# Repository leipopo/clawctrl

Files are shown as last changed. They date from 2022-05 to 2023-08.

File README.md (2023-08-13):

# An end effector 

using a specific protocol（see in code file） on uart to control a four fingers hand moving to a certain position or use a constant force to garb a object

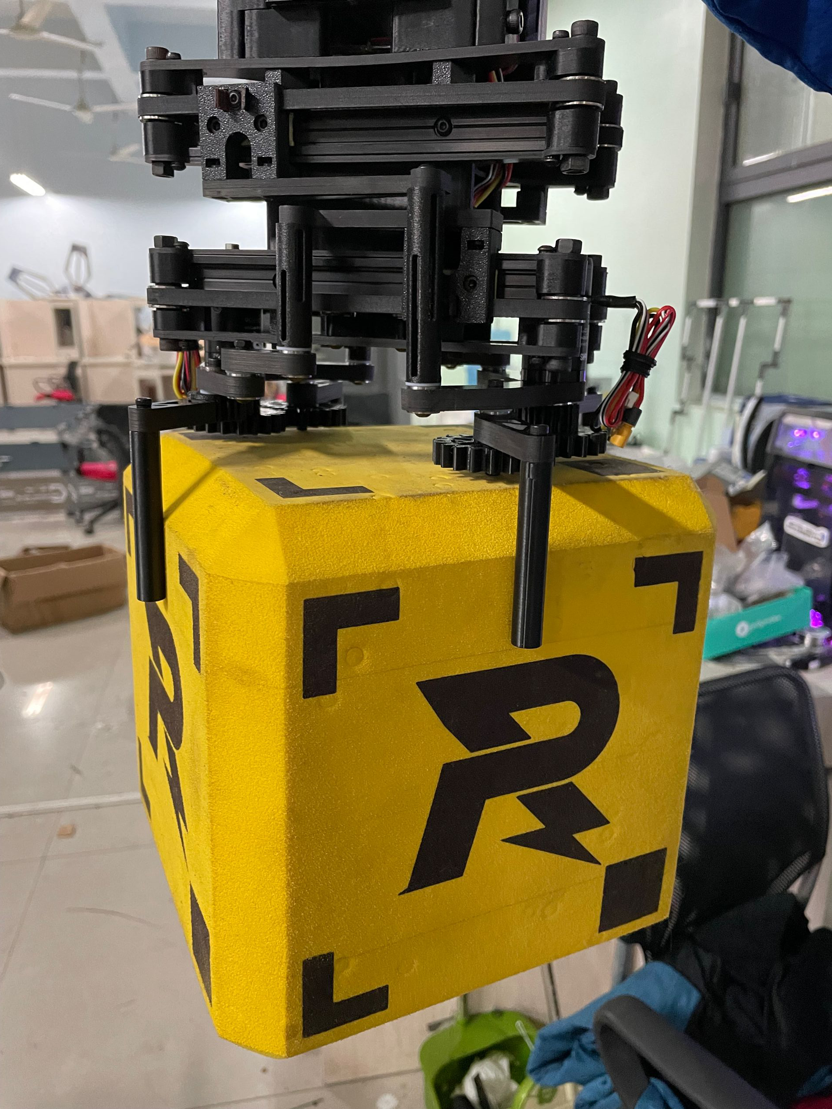
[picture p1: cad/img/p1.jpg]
claw with a RoboMaster gold ore without ctrl


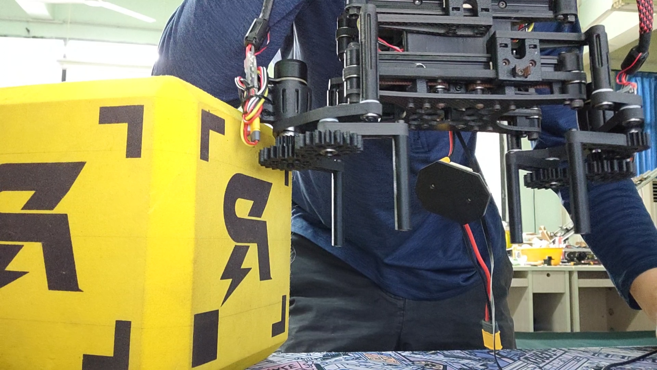
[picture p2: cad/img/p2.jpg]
claw with a RoboMaster gold ore


# Built with 
RoboMaster m2006&c610 kit

3d_printed abs and pet-cf (filament from Fusrock)

cnc carbon fibre sheet 
            
# Coded on 
a stm32(RoboMaster aboard with f427) with MDK and cubemx 

# Content

cad contains .stp and .stl

code contains code generated by cubemx

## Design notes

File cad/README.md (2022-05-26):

# content
## process（除张紧臂及（mir）外，全部一式两份，张紧臂及（mir）四份）
- v3打印件： 打印件stl文件 
            打印件设计优化过 使用fdm工艺打印不需要添加支撑
            stl已放置至合适方向 
            建议壁厚大于2mm 填充大于百分之三十 直线或网格填充
- v3板件：板件step文件 有沉孔 须向加工商注明
- bom表：还没写

## cad 
- lastest version step and f3d

## img
- some imgs.jpg

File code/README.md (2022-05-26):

# 参数单位：（详见config.h）
- 角度：deg
- 转速：rpm
- 电流：A
- 转矩：N·m
- 时间：ms
- 频率：Hz

# 电机定义：
- 手指电机为电机一与电机二
- 手掌电机为电机三（远离手指）和电机四（靠近手指）

# 基本通讯：
## PCtoMCU：

|Data[0]|Data[1]|Data[2]|Data[3]|Data[4]|Data[5]|Data[6]|Data[7]|Data[8]|Data[9]|Data[10]|Data[11]| 功 能  |
|:----:|:----:|:----:|:----:|:----:|:----:|:----:|:----:|:----:|:----:|:----:|:----:|:----:|
|0x00|电机一相对角度改变值高八位|电机一相对角度改变值低八位|电机二相对角度改变值高八位|电机二相对角度改变值低八位|电机三相对角度改变值高八位|电机三相对角度改变值低八位|电机四相对角度改变值高八位| 电机四相对角度改变值低八位| 暂无校验| 暂无校验| 0x0A|设定电机相对角度|
|0x01|电机一绝对角度值高八位|电机一绝对角度值低八位|电机二绝对角度值高八位|电机二绝对角度值低八位|电机三绝对角度值高八位|电机三绝对角度值低八位|电机四绝对角度值高八位|电机四绝对角度值低八位| 暂无校验| 暂无校验| 0x0A|设定电机绝对角度|
|0x02|电机一速度设定值高八位|电机一速度设定值低八位|电机二速度设定值高八位|电机二速度设定值低八位|电机三速度设定值高八位|电机三速度设定值低八位|电机四速度设定值高八位|电机四速度设定值低八位| 暂无校验| 暂无校验| 0x0A|设定电机最大转速|
|0x03|电机一转矩值X10高八位|电机一转矩值X10低八位|电机二转矩值X10高八位|电机二转矩值X10低八位|电机三转矩值X10高八位|电机三转矩值X10低八位|电机四转矩值X10高八位|电机四转矩值X10低八位| 暂无校验| 暂无校验| 0x0A|设定电机转矩|
|0x04|0x00|0x00|0x00|0x00|0x00|0x00|0x00| 0x00| 暂无校验| 暂无校验| 0x0A|放松|
|0x05|0x00|0x00|0x00|0x00|0x00|0x00|0x00| 0x00| 暂无校验| 暂无校验| 0x0A|回零|
|0xff|0x00|0x00/0x01|0x00|0x00/0x01|0x00|0x00/0x01|0x00| 0x00/0x01| 0x0/10/10/10/1| 0x0/10/10/10/1| 0x0A|关电机|

**注：电机控制方式是同时变化的，**即爪子四个电机只能同时以绝对角度或者相对角度或者转矩控制，且只能同时放松或回零。
具体状态转换见（infoproc.c/infoproc.h，
  
`void command2clawinfo(usercommand *uc,clawinfo *ci,MotorInfo m[4])`，

`void motor2clawinfo(clawinfo *ci,MotorInfo m[4])`，

`void claw2motorinfo(clawinfo *ci,MotorInfo m[4])`)。

**电机通断电可以单独控制，** 如单独断开电机二的电流需输入0xff 0x00 0x01（电机一通电）0x00 0x00（电机二断电）0x00 0x01（电机三通电） 0x00 0x01（电机四通电） 0x10 0x11（校验） 0x0a，具体转换详见（uart3.c/uart3.h，

`void RX_Decoder(uint8_t *buf, usercommand *uc)`）。

串口接收见（uart3.c/uart3.h，
  
`void RX_Decoder(uint8_t *buf, usercommand *uc)`）。

## MCUtoPC：
### 数据回报：
- 状态定义：
- 爪子状态：0x00 rel_postionctrl 0x01 abs_postionctrl 0x02 torquectrl 0x03 loose 0x04 zero 0x05 ready 0x06 moving
- 电机状态：0x00 loose 0x01 zeroing 0x10 inpostion 0x11 moving

|Data[0]|Data[1]|Data[2]|Data[3]|Data[4]|Data[5]|Data[6]|Data[7]|Data[8]|Data[9]|Data[10]|Data[11]| 功 能  |
|:----:|:----:|:----:|:----:|:----:|:----:|:----:|:----:|:----:|:----:|:----:|:----:|:----:|
|0xf0|0x00|电机一状态|0x00|电机二状态|0x00|电机三状态|0x00| 电机四状态| 0x00| 爪子状态| 0x0A|回报电机当前状态和爪子状态|
|0xf1|当前电机一转矩X100高八位|当前电机一转矩X100低八位|当前电机二转矩X100高八位|当前电机二转矩X100低八位|当前电机三转矩X100高八位|当前电机三转矩X100低八位|当前电机四转矩X100高八位|当前电机四转矩X100低八位| 四电机转矩X100加和高八位| 四电机转矩X100加和高八位| 0x0A|回报电机当前转矩X100|
|0xf2|当前电机一角度高八位|当前电机一角度低八位|当前电机二角度高八位|当前电机二角度低八位|当前电机三角度高八位|当前电机三角度低八位|当前电机四角度高八位|当前电机四角度低八位| 四电机角度加和高八位| 四电机角度加和低八位| 0x0A|回报电机当前角度|
|0xf3|当前电机一速度高八位|当前电机一速度低八位|当前电机二速度高八位|当前电机二速度低八位|当前电机三速度高八位|当前电机三速度低八位|当前电机四速度高八位|当前电机四速度低八位| 四电机转速加和高八位| 四电机转速加和低八位| 0x0A|回报电机当前转速|

### 警告回报：

|Data[0]|Data[1]|Data[2]|Data[3]|Data[4]|Data[5]|Data[6]|Data[7]|Data[8]|Data[9]|Data[10]|Data[11]|
|:----:|:----:|:----:|:----:|:----:|:----:|:----:|:----:|:----:|:----:|:----:|:----:|
|0xaa|手掌电机差角过大警告|电机位置控制转警告高八位|电机位置控制转警告低八位|0x00|0x00|0x00|0x00|0x00|0x00|0x00|0x0a|

**注：在对手掌电机差角的判断中若电机三角度大于电机四（以回零的方向为正）则反馈0x10，反之为0x01，正常为0x00；
在对电机=堵转的判断中，若电机二堵转则反馈0x0100，正常为0x0000**

内容详见（infoproc.c/infoproc.h，

`void sendmestopc(void)`)。

电机控制算法详见（motorlib.c/motorlib.h）。

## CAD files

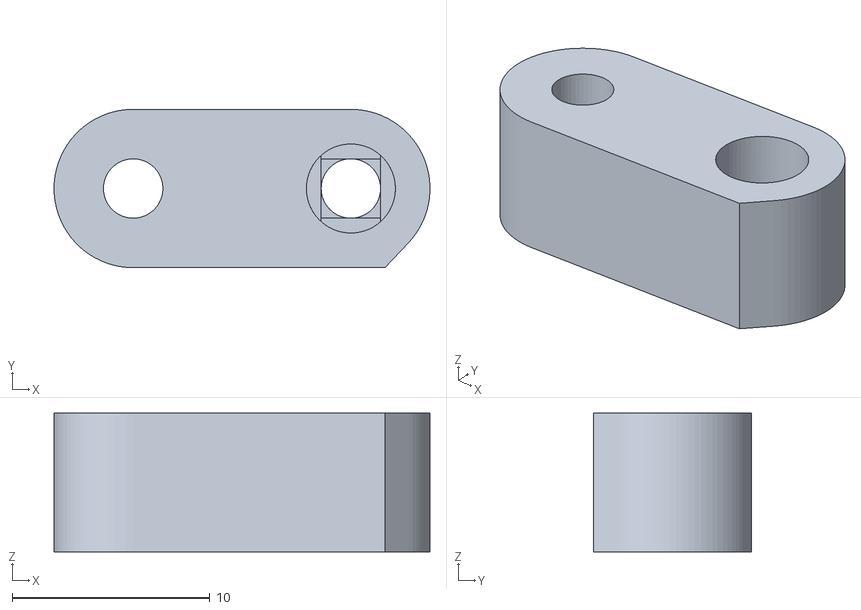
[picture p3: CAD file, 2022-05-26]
cad/prosfile/V3打印件/新张紧臂（mir） v2.stl
19.0 x 8.00 x 7.00

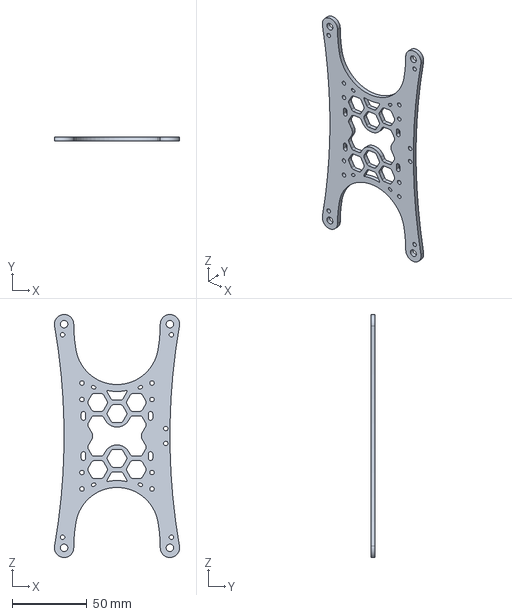
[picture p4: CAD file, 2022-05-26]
cad/prosfile/V3板件/上板 v11.step
84.0 x 3.00 x 163.0 mm

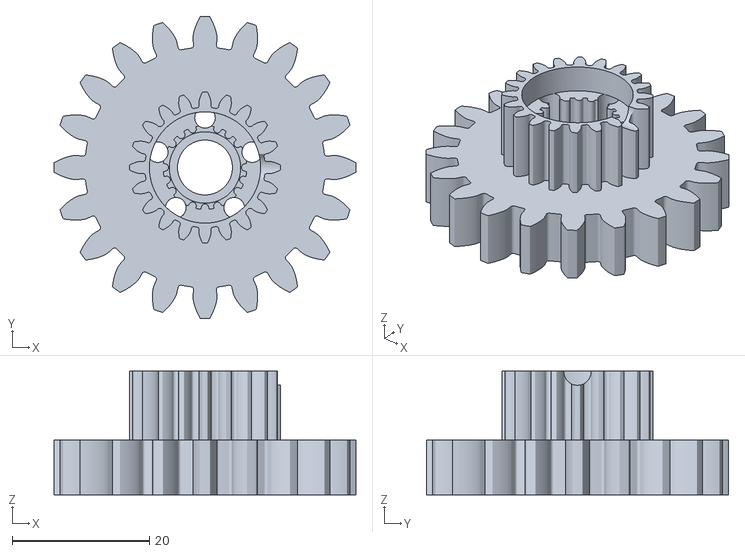
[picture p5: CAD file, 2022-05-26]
cad/prosfile/V3打印件/1_20&2_20驱动齿 v5.stl
44.0 x 44.0 x 18.0

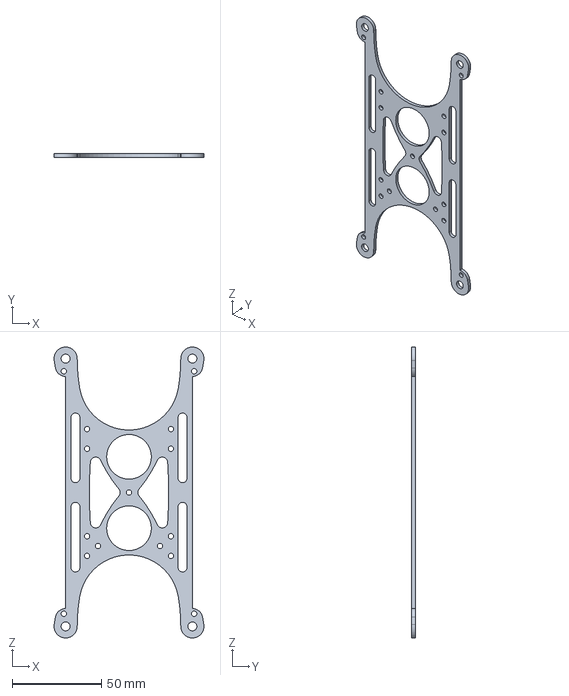
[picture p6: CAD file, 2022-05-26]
cad/prosfile/V3板件/下板 v13.step
84.0 x 2.00 x 163.0 mm

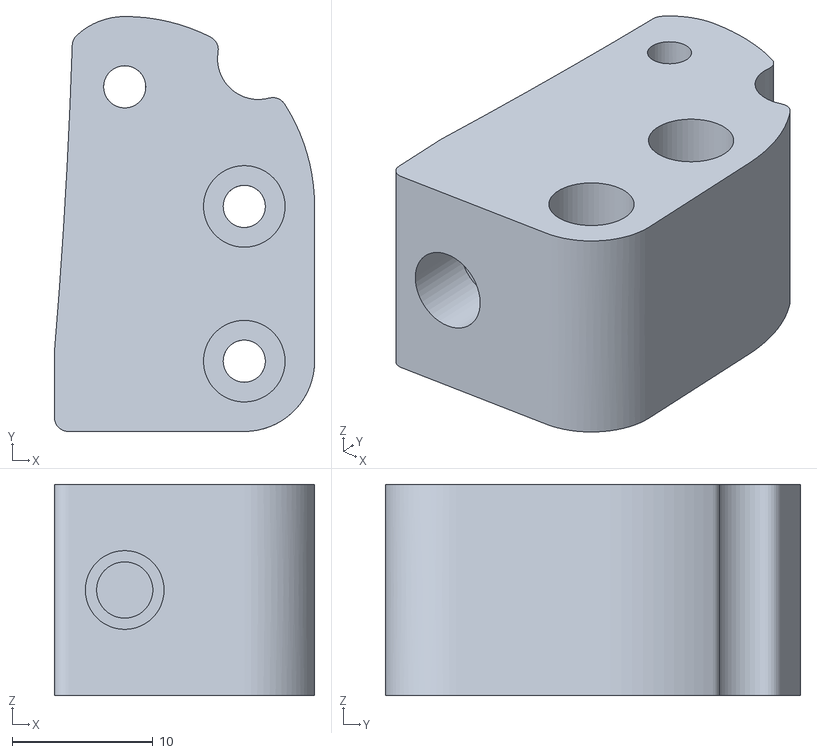
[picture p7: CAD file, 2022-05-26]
cad/prosfile/V3打印件/锚点 v4.stl
18.5 x 29.5 x 15.0

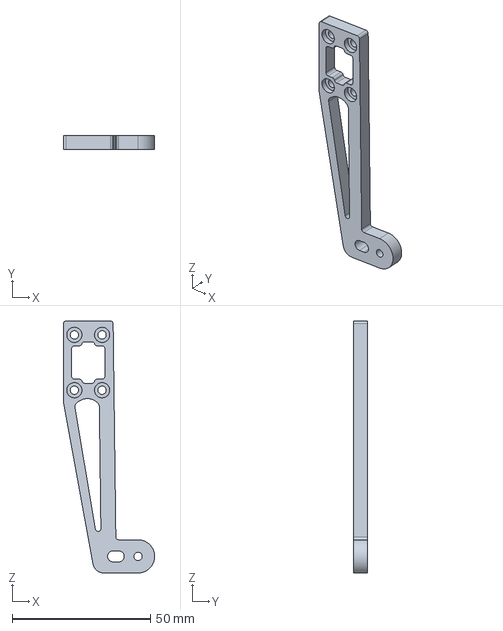
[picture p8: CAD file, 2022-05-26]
cad/prosfile/V3板件/效应器推杆 v13.step
33.0 x 5.00 x 91.0 mm

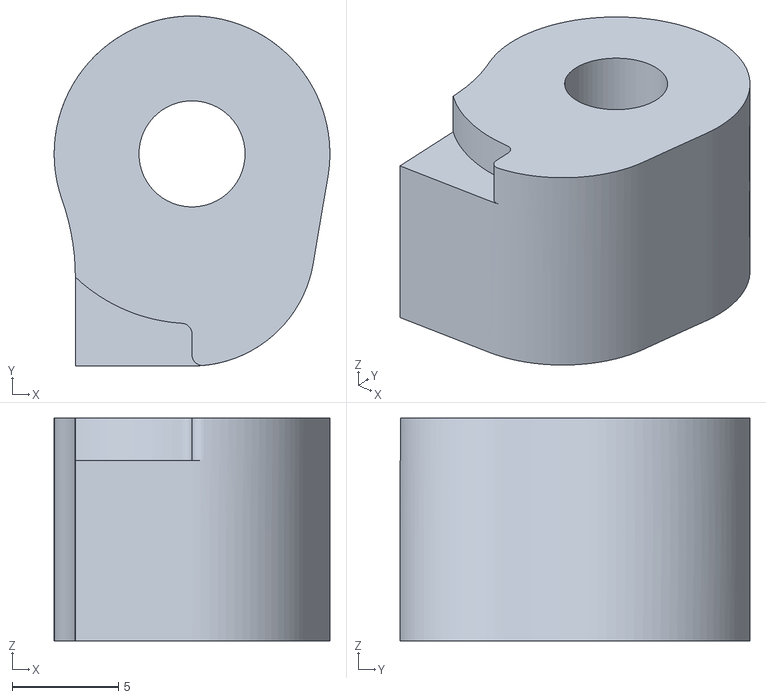
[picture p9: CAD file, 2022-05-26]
cad/prosfile/V3打印件/同步带角导向下mirror v2.stl
13.0 x 16.5 x 10.5

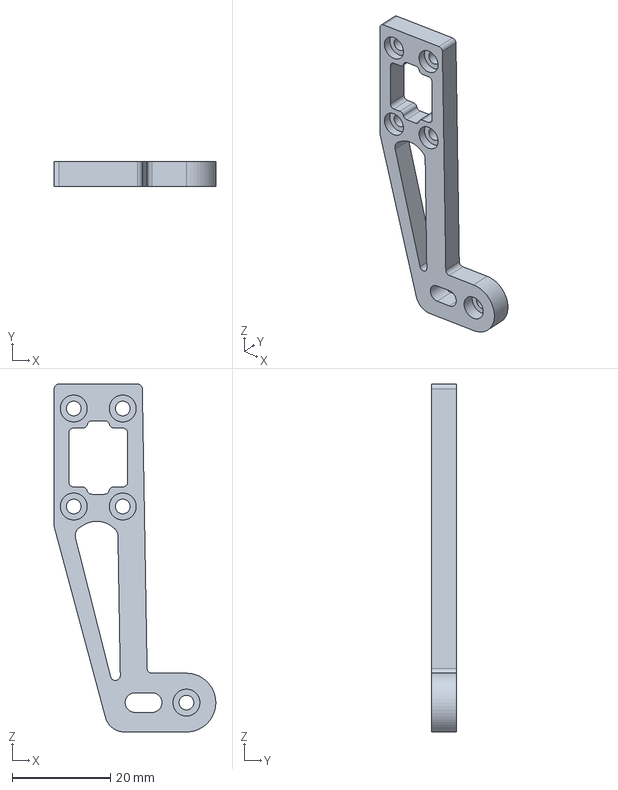
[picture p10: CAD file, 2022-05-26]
cad/prosfile/V3板件/效应器摇臂推杆 v13.step
33.0 x 5.00 x 71.0 mm

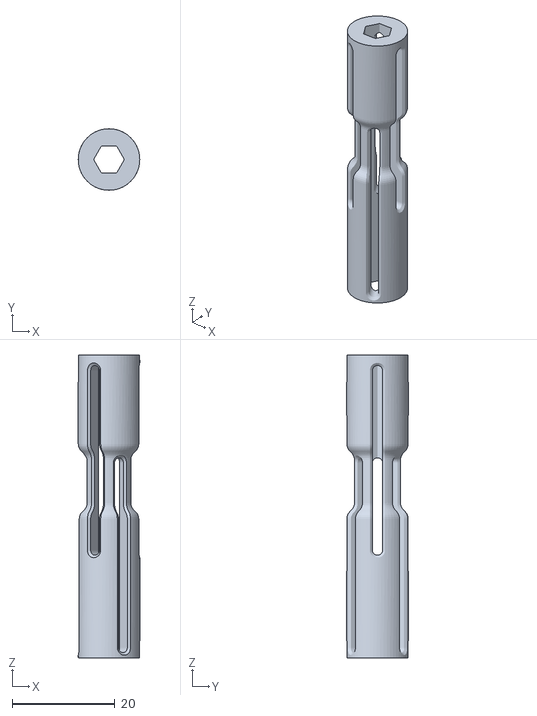
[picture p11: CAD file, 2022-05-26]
cad/prosfile/V3打印件/效应器推杆z柱 v15.stl
12.0 x 12.0 x 59.1

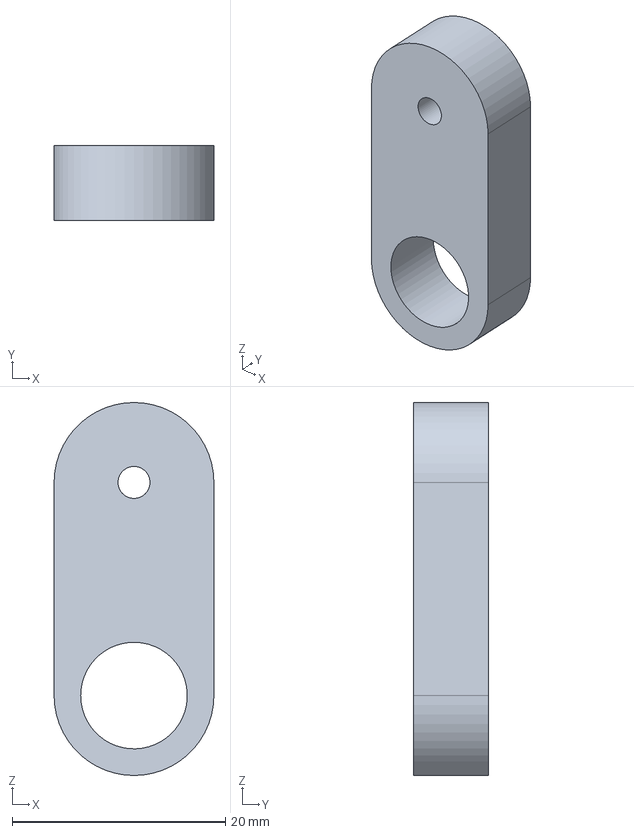
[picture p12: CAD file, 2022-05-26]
cad/prosfile/V3板件/效应器摇臂_x2_7mm.step
15.0 x 7.00 x 35.0 mm

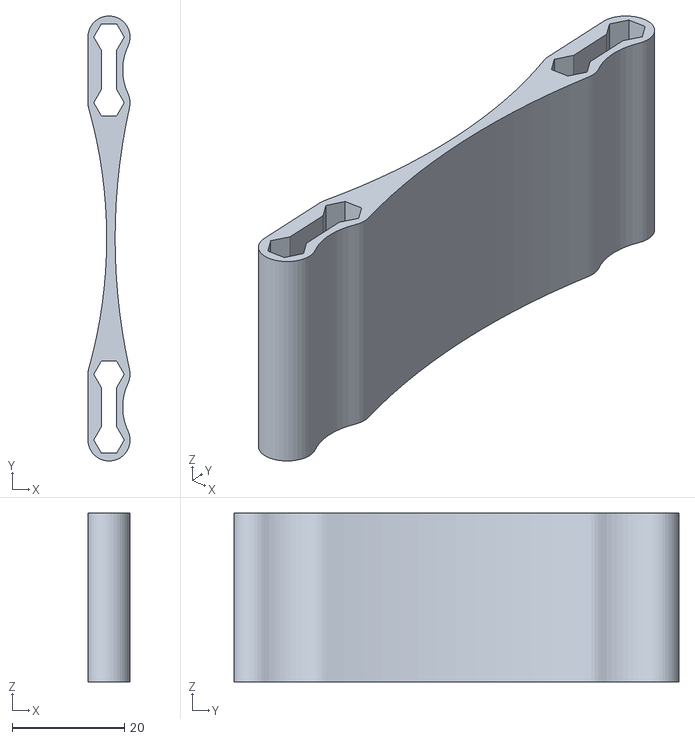
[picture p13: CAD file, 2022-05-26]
cad/prosfile/V3打印件/机架支座 v13.stl
7.50 x 79.2 x 30.0

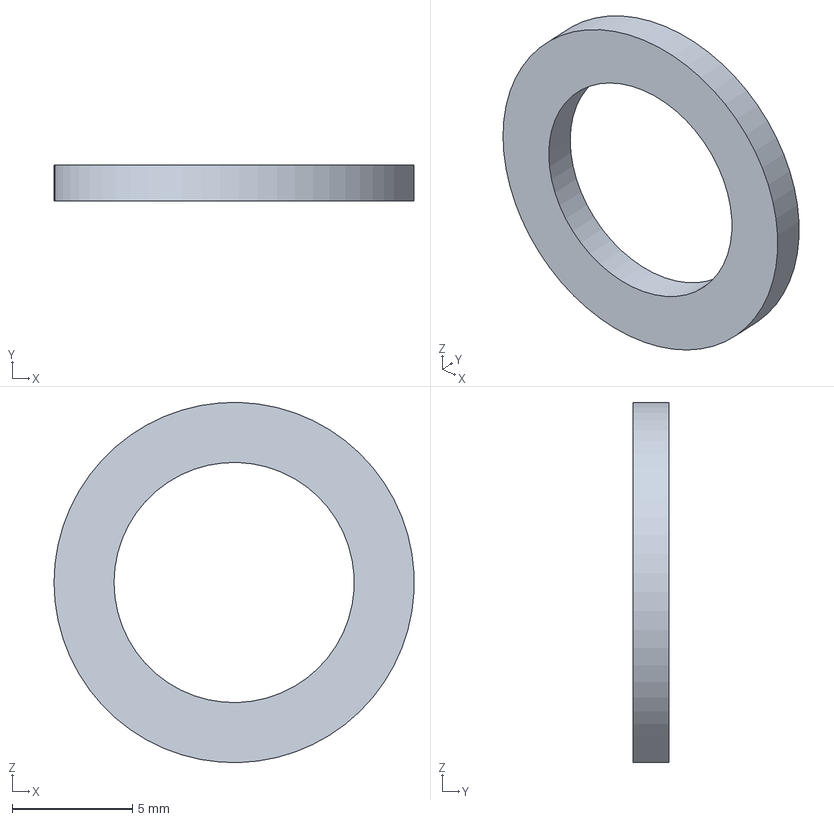
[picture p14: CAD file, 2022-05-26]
cad/prosfile/V3板件/1.45_10_15垫高_x2_1.5mm.step
15.0 x 1.50 x 15.0 mm

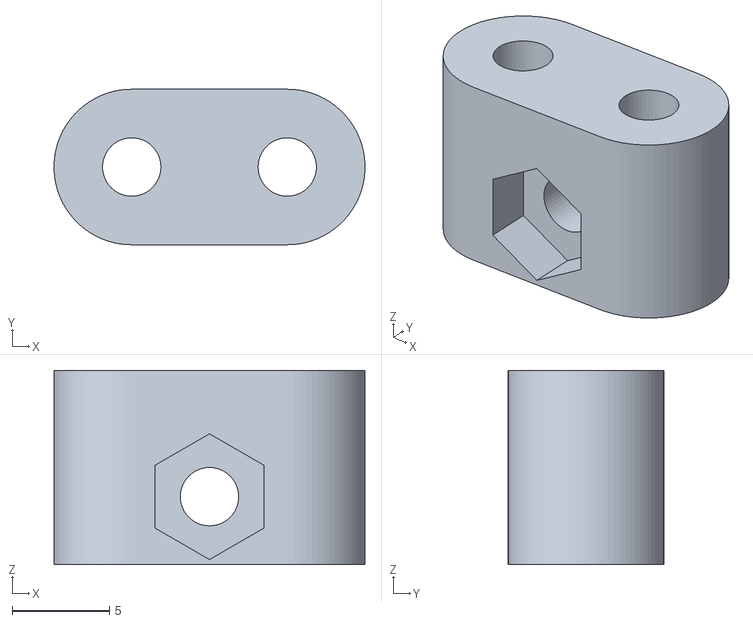
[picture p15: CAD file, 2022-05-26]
cad/prosfile/V3打印件/新张紧主体(带螺母) v4.stl
16.0 x 8.00 x 10.0

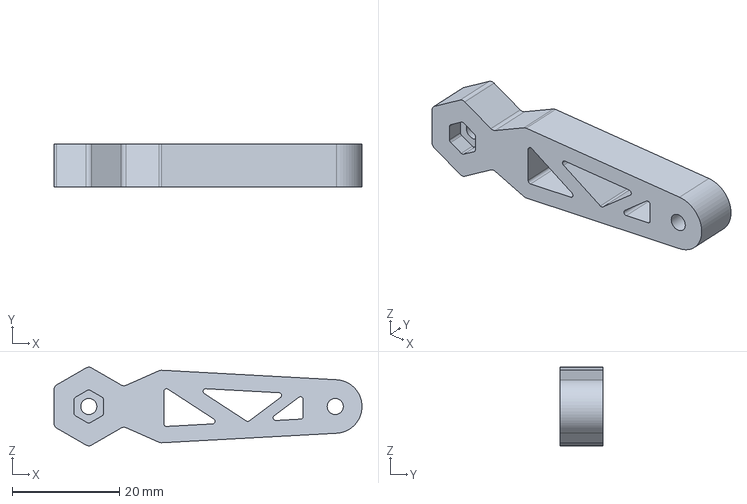
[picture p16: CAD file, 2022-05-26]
cad/prosfile/V3板件/40mm手指B_x2_8mm.step
57.5 x 8.00 x 14.7 mm

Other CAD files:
cad/prosfile/V3打印件/定位销 v1.stl
cad/prosfile/V3板件/40mm手指A_x2_8mm.step
cad/prosfile/V3打印件/1_20转向齿 v7.stl
cad/prosfile/V3板件/新效应器主架板_x2_7mm.step
cad/prosfile/V3打印件/1_20手指齿 v10.stl
cad/prosfile/V3打印件/2006机架电机座 v9.stl
cad/prosfile/V3打印件/2_20手指齿 v25.stl
cad/prosfile/V3打印件/GPA40GT2060-A-H6 v2.stl
cad/prosfile/V3打印件/同步带角导向上 v8.stl
cad/prosfile/V3打印件/同步带角导向上mirror v2.stl
cad/prosfile/V3打印件/同步带角导向下 v6.stl
cad/prosfile/V3打印件/开口带夹紧 v11.stl
cad/prosfile/V3打印件/开口连接座 v22.stl
cad/prosfile/V3打印件/手指 v9.stl
cad/prosfile/V3打印件/效应器摇臂推杆z柱 v13.stl
cad/prosfile/V3打印件/新张紧主体 v5.stl
cad/prosfile/V3打印件/新张紧臂 v7.stl
cad/prosfile/V3打印件/新张紧臂上 v2.stl
cad/prosfile/V3打印件/新张紧臂上（mir） v2.stl
cad/prosfile/V3打印件/轨道支架a v9.stl
cad/prosfile/V3打印件/轨道支架b v2.stl
cad/prosfile/V3打印件/连接器 v12.stl
cad/prosfile/V3打印件/锚点（mir） v4.stl
cad/prosfile/V3打印件/闭口连接座 v14.stl

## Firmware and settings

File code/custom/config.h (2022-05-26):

#ifndef CFG_H
#define CFG_H

/*单位
角度：°
转速：rpm
电流：A
转矩：N·m
时间：ms
频率：Hz

*/

#define task_period 2
#define zeromotoranglespeed  30.f
#define maxanglespeed 500.f
#define maxcurrentvalue 10000.f
#define maxcurrent 10.f
#define reductionratio 36.f
#define maxfingerangle 230.f
#define minfingerangle -230.f
#define maxpalmangle 460.f 
#define minpalmangle -460.f
#define maxpalmdifangle 0.f
#define safecurrentcoe 0.4f
#define tccoe 3.f
#define ctcoe 1.f/tccoe

#define tp task_period 
#define zas zeromotoranglespeed  
#define maxas maxanglespeed 
#define maxfa maxfingerangle
#define minfa minfingerangle
#define maxpa maxpalmangle
#define minpa minpalmangle


#define finger1_default_config \
{ \
	{ \
		{minfa,maxfa}, \
		maxas, \
		{maxcurrentvalue,maxcurrent}, \
		ctcoe, \
		reductionratio, \
		0.f, \
		0.f, \
		2, \
		0x1,\
		-1,\
		1,\
	}, \
	{ \
		0.f, \
		0.f, \
		0.f, \
		0.f, \
		0.f, \
		{0.f,0.f}, \
	}, \
	{ \
		0.f, \
		0.f, \
		0.f, \
	}, \
	{ \
		0.f, \
		0.f, \
		{0.f,0.f,0.f,0.f,0.f}, \
	}, \
} \

#define finger2_default_config \
{ \
	{ \
		{minfa,maxfa}, \
		maxas, \
		{maxcurrentvalue,maxcurrent}, \
		ctcoe, \
		reductionratio, \
		0.f, \
		0.f, \
		2, \
		0x1,\
		-1,\
		1,\
	}, \
	{ \
		0.f, \
		0.f, \
		0.f, \
		0.f, \
		0.f, \
		{0.f,0.f}, \
	}, \
	{ \
		0.f, \
		0.f, \
		0.f, \
	}, \
	{ \
		0.f, \
		0.f, \
		{0.f,0.f,0.f,0.f,0.f}, \
	}, \
} \

#define palm1_default_config \
{ \
	{ \
		{minpa,maxpa}, \
		maxas, \
		{maxcurrentvalue,maxcurrent}, \
		ctcoe, \
		reductionratio, \
		0.f, \
		0.f, \
		2, \
		0x1,\
		-1,\
		1,\
	}, \
	{ \
		0.f, \
		0.f, \
		0.f, \
		0.f, \
		0.f, \
		{0.f,0.f}, \
	}, \
	{ \
		0.f, \
		0.f, \
		0.f, \
	}, \
	{ \
		0.f, \
		0.f, \
		{0.f,0.f,0.f,0.f,0.f}, \
	}, \
} \

#define palm2_default_config \
{ \
	{ \
		{minpa,maxpa}, \
		maxas, \
		{maxcurrentvalue,maxcurrent}, \
		ctcoe, \
		reductionratio, \
		0.f, \
		0.f, \
		2, \
		0x1,\
		1,\
		-1,\
	}, \
	{ \
		0.f, \
		0.f, \
		0.f, \
		0.f, \
		0.f, \
		{0.f,0.f}, \
	}, \
	{ \
		0.f, \
		0.f, \
		0.f, \
	}, \
	{ \
		0.f, \
		0.f, \
		{0.f,0.f,0.f,0.f,0.f}, \
	}, \
} \

#define finger_angle_pid \
{ \
	0.f, \
	0.f, \
	{0.f,0.f}, \
	0.f, \
	0.f, \
	0.f, \
	0.f, \
	0.f, \
	0.f, \
	zeromotoranglespeed, \
	zeromotoranglespeed, \
	zeromotoranglespeed, \
	0.f, \
	zeromotoranglespeed, \
} \

#define finger_speed_pid \
{ \
	0.f, \
	0.f, \
	{0.f,0.f}, \
	0.f, \
	0.f, \
	0.f, \
	0.f, \
	0.f, \
	0.f, \
	safecurrentcoe*maxcurrentvalue, \
	safecurrentcoe*maxcurrentvalue, \
	safecurrentcoe*maxcurrentvalue, \
	0.f, \
	safecurrentcoe*maxcurrentvalue, \
} \

#define palm_angle_pid \
{ \
	0.f, \
	0.f, \
	{0.f,0.f}, \
	0.f, \
	0.f, \
	0.f, \
	0.f, \
	0.f, \
	0.f, \
	zeromotoranglespeed, \
	zeromotoranglespeed, \
	zeromotoranglespeed, \
	0.f, \
	zeromotoranglespeed, \
} \

#define palm_speed_pid \
{ \
	0.f, \
	0.f, \
	{0.f,0.f}, \
	0.f, \
	0.f, \
	0.f, \
	0.f, \
	0.f, \
	0.f, \
	safecurrentcoe*maxcurrentvalue, \
	safecurrentcoe*maxcurrentvalue, \
	safecurrentcoe*maxcurrentvalue, \
	0.f, \
	safecurrentcoe*maxcurrentvalue, \
} \





#endif

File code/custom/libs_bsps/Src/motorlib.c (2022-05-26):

#include "main.h"

/*-------------------------------------
* 函数名：测试用波形发生器
* 描述  ：波形发生器
* 输入  ：dddd
* 输出  ：dddd
作者：LPGUAIA
日期：2021.7.7
-----------------------------------------*/
wave_HandleTypeDef sinwave={0x01,\
														1000,\
														5,\
														90};

float wavegenerator (wave_HandleTypeDef *SinWave)
{
	uint16_t samplenum = SinWave->waveperiod/SinWave->taskperiod;
	static uint16_t count;
	float output;
	
	if(count<samplenum)
		count++;
	else
		count=0;
	
	switch(SinWave->wavetpye)
	{
		case asinwave:
			output=SinWave->amplitude*sin(2*PI*count/samplenum);break;
		case atriwave:
			output=SinWave->amplitude*count/samplenum;break;
		case stepwave:
			output=SinWave->amplitude*((int)((2*count-1)/samplenum));break;
		default:
			output=SinWave->amplitude*sin(2*PI*count/samplenum);break;
	}
	
	return output;
}



/*-------------------------------------
* 函数名：减速电机角度解算
* 描述  ：计算减速后的角度
* 输入  ：电机结构体
* 输出  ：无

作者：LPGUAIA
日期：2021.4.27
-----------------------------------------*/ 

void gearmotor_angledecoder(MotorInfo *Motor)
{
	
	Motor->tempdata.anglechanged=Motor->tempdata.temp_angle[1] - Motor->tempdata.temp_angle[0];
	Motor->tempdata.temp_angle[0]=Motor->tempdata.temp_angle[1];
	
	
	if(ABS(Motor->tempdata.anglechanged)<=300)
		Motor->tempdata.anglechanged=Motor->tempdata.anglechanged/Motor->parameter.reductiongearratio;
	else if(Motor->tempdata.anglechanged>300)
		Motor->tempdata.anglechanged = (Motor->tempdata.anglechanged-360) / Motor->parameter.reductiongearratio;
	else if(Motor->tempdata.anglechanged<-300)
		Motor->tempdata.anglechanged = (360 + Motor->tempdata.anglechanged) / Motor->parameter.reductiongearratio;
	
	
	if(ABS(Motor->tempdata.anglechanged + Motor->curmotorinfo.angle)<180)
		Motor->curmotorinfo.angle = Motor->tempdata.anglechanged + Motor->curmotorinfo.angle;
	else if(Motor->tempdata.anglechanged + Motor->curmotorinfo.angle<=-180)
		Motor->curmotorinfo.angle = Motor->tempdata.anglechanged + Motor->curmotorinfo.angle + 360;
	else if(Motor->tempdata.anglechanged + Motor->curmotorinfo.angle>=180)
		Motor->curmotorinfo.angle = Motor->tempdata.anglechanged + Motor->curmotorinfo.angle - 360;
}
/*-------------------------------------
* 函数名：减速电机角度解算
* 描述  ：计算减速后的累计角度
* 输入  ：电机结构体
* 输出  ：无

作者：LPGUAIA
日期：2021.4.27
-----------------------------------------*/ 
void gearmotor_angledecoder_sum(MotorInfo *Motor)
{
	
	Motor->tempdata.anglechanged=Motor->tempdata.temp_angle[1] - Motor->tempdata.temp_angle[0];
	Motor->tempdata.temp_angle[0]=Motor->tempdata.temp_angle[1];
	
	
	if(ABS(Motor->tempdata.anglechanged)<=300)
		Motor->tempdata.anglechanged=Motor->tempdata.anglechanged/Motor->parameter.reductiongearratio;
	else if(Motor->tempdata.anglechanged>300)
		Motor->tempdata.anglechanged = (Motor->tempdata.anglechanged-360) / Motor->parameter.reductiongearratio;
	else if(Motor->tempdata.anglechanged<-300)
		Motor->tempdata.anglechanged = (360 + Motor->tempdata.anglechanged) / Motor->parameter.reductiongearratio;
	
		Motor->curmotorinfo.angle = Motor->tempdata.anglechanged + Motor->curmotorinfo.angle;

}

/*-------------------------------------
* 函数名：角度跟速度环计算
* 描述  ：角度跟速度环的简单计算
* 输入  ：电机结构体，角度和速度pid结构体
* 输出  ：无

作者：LPGUAIA
日期：2022.4
-----------------------------------------*/ 

void motaspid_calc(MotorInfo *minfo,PID_regulator *anglepid,PID_regulator *speedpid)
{
	
	if(minfo->tempdata.pidcount<minfo->parameter.pidoutcycrate&&minfo->tempdata.pidcount>=0)
		minfo->tempdata.pidcount++;
	else
		minfo->tempdata.pidcount=0;
	
	
	if(minfo->tempdata.pidcount==minfo->parameter.pidoutcycrate)
	{
		
		anglepid->tar=minfo->tarmotorinfo.angle;
		anglepid->cur=minfo->curmotorinfo.angle;
		anglepid->outputMax=minfo->tarmotorinfo.speed;
		PID_angle_calc(anglepid,1,300);
		minfo->tempdata.pidcount=0;
	}
		
		speedpid->tar=anglepid->output;
		speedpid->cur=minfo->curmotorinfo.speed;
	
		PID_calc(speedpid,1);
}
/*-------------------------------------
* 函数名：电机电流感应
* 描述  ：更新电流数据，保存五次采样值
* 输入  ：电机结构体
* 输出  ：无

作者：LPGUAIA
日期：2022.4
-----------------------------------------*/ 
void motcurrentsensor(MotorInfo *minfo)
{
	
	for(uint8_t i=4;i>0;i--)
	{
		minfo->curmotorinfo.current[i]=minfo->curmotorinfo.current[i-1];
	}
	for(int8_t i=4;i>=0;i--)
	{
		minfo->tempdata.currentsum+=ABS(minfo->curmotorinfo.current[i]);
	}
	if(ABS(minfo->curmotorinfo.current[0])>=minfo->parameter.inpositioncurrent&&ABS(minfo->curmotorinfo.current[1])>=minfo->parameter.inpositioncurrent)\
	{
		minfo->tempdata.angle=minfo->curmotorinfo.angle;
	}
}
/*-------------------------------------
* 函数名：can解码成电机数据
* 描述  ：将can的数据解算成电机数据
* 输入  ：电机结构体，can的数据
* 输出  ：无

作者：LPGUAIA
日期：2022.4
-----------------------------------------*/ 
void canrxtomotinfo(MotorInfo *minfo,uint8_t rx[8])
{
	
	
		minfo->tempdata.temp_angle[1] = ((int16_t)minfo->parameter.reversed*((rx[0]<<8)|(rx[1])))*360.0f/0x1fff-180.f;
		if(minfo->parameter.sumangle)
			gearmotor_angledecoder_sum(minfo);
		else
			gearmotor_angledecoder(minfo);
		minfo->curmotorinfo.speed = ((int16_t)(minfo->parameter.reversed*((rx[2]<<8)|(rx[3]))))/minfo->parameter.reductiongearratio;
		motcurrentsensor(minfo);
		minfo->curmotorinfo.current[0] = ((int16_t)(minfo->parameter.reversed*((rx[4]<<8)|(rx[5]))))/(minfo->parameter.current_limit[0])*minfo->parameter.current_limit[1];

}

float anglecircle(float angle)
{
	while(angle>180.f)
	{
		angle=angle-360.f;
	}
	while(angle<-180.f)
	{
		angle=angle+360.f;
	}

	return angle;
}

float anglelimit(float angle,float anglemax,float anglemin)
{
	return LIMIT(angle,anglemin,anglemax);
}

float currentlimit(float current,float currentmax)
{
	return LIMIT(current,-currentmax,currentmax);;
}

float speedlimit(float speed,float speedmax)
{
	return MIN( speed,speedmax );
}

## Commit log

2022-05-26 move code to file "code" to add file for cad
2022-05-26 add cad and process file
    [1.45_10_15垫高_x2_1.5mm.step, 1_20&2_20驱动齿 v5.stl, 1_20手指齿 v10.stl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]
2022-05-26 add cad file and move codes to code
2022-05-26 optimized 3d_print parts and place .stl in a better place
    [1_20&2_20驱动齿 v5.stl, 1_20手指齿 v10.stl, 1_20转向齿 v7.stl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]
2022-05-30 added iwdg and fixed the failure of soft limit
    [canbus.c, clawctrl_v3.ioc, infoproc.c]
2022-08-24 打了个螺丝
